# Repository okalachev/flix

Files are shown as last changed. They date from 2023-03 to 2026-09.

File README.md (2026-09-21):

<!-- markdownlint-disable MD041 -->

<p align="center">
  Flix logo<br>
  <b>Flix</b> (<i>flight + X</i>) — open source ESP32-based quadcopter made from scratch.
</p>

<table>
  <tr>
    <td align=center><strong>Version 1.1</strong> (3D-printed frame)</td>
    <td align=center><strong>Version 0</strong></td>
  </tr>
  <tr>
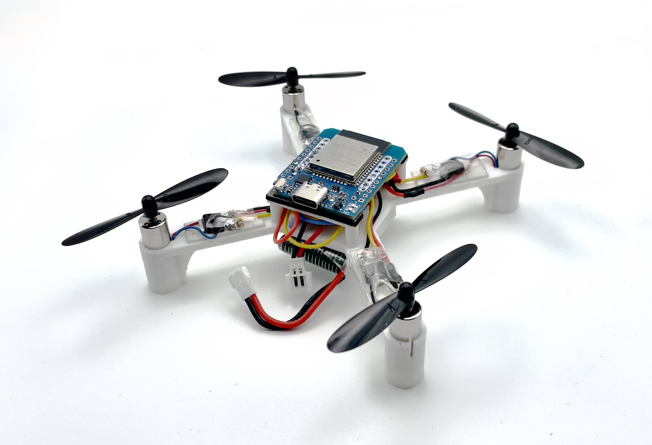
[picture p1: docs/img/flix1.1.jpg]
Flix quadcopter
    <td></td>
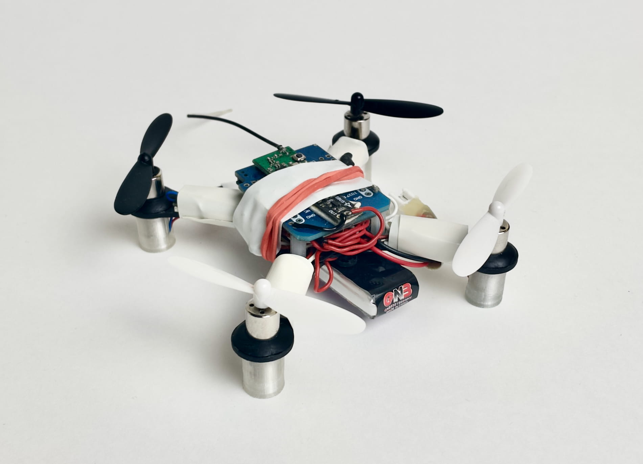
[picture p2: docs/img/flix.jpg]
Flix quadcopter
    <td></td>
  </tr>
</table>

## Features

* Dedicated for education and research.
* Made from general-purpose components.
* Simple and clean source code in Arduino (<2k lines firmware).
* Communication using MAVLink protocol over Wi-Fi or ESP-NOW.
* Control with USB gamepad, remote control or smartphone.
* Wireless command line interface and analyzing.
* Precise simulation with Gazebo.
* Python library for scripting and automatic flights.
* Textbook on flight control theory and practice ([in development](https://quadcopter.dev)).
* *Position control (planned)*.

## It actually flies

See detailed demo video: https://youtu.be/hT46CZ1CgC4.



Version 0 demo video: https://youtu.be/8GzzIQ3C6DQ.



Usage in education (RoboCamp 2025): https://youtu.be/Wd3yaorjTx0.



See the [user builds gallery](docs/user.md):

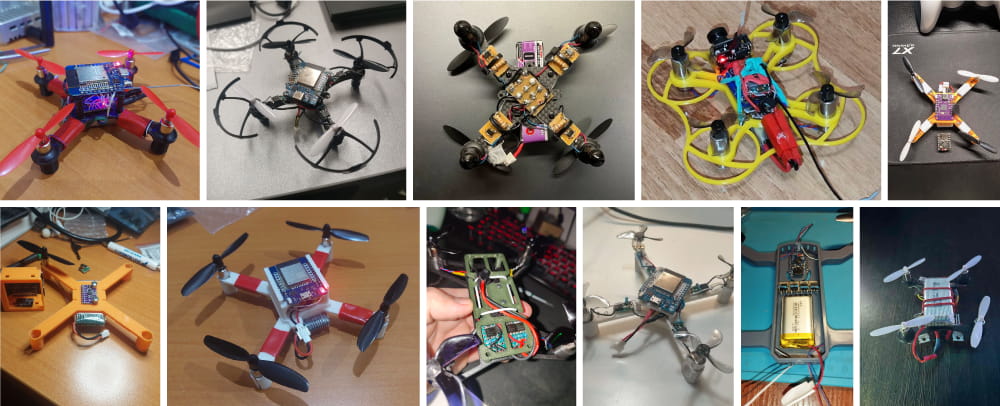
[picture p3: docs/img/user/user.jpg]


### PCB

The official PCB *(Flix2)* is in development now. Follow the [project's channel](https://t.me/opensourcequadcopter) to track the progress.

Outdoor flights demo video of the current prototype:



### Position control

The position control feature is in development. RoboCamp 2026 demo (using an overhead camera, [sources](https://github.com/xTimop/flix-poscontrol/compare/robolager2026...xTimop:flix-poscontrol:poscontrol)):



## Simulation

The simulator is implemented using Gazebo and runs the original Arduino code:

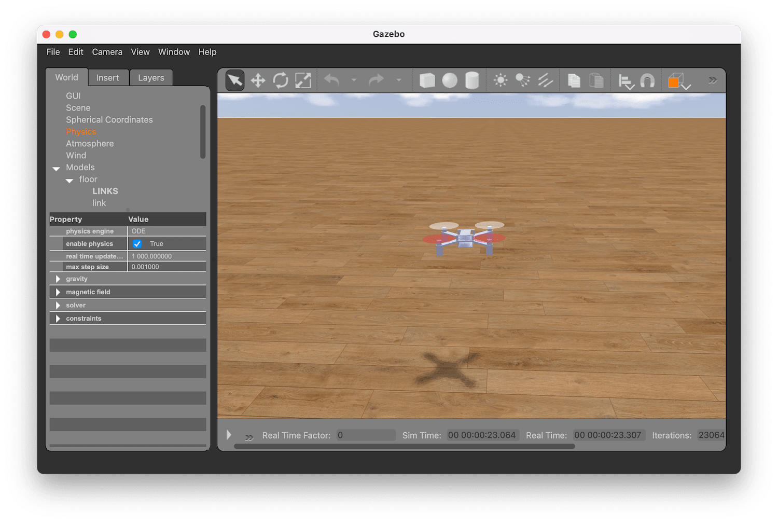
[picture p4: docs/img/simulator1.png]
Flix simulator


## Documentation articles

1. [Assembly instructions](docs/assembly.md).
2. [Usage: build, setup and flight](docs/usage.md).
3. [Simulation](gazebo/README.md).
4. [Python library](tools/pyflix/README.md).

Additional articles:

* [User builds gallery](docs/user.md).
* [Firmware architectural overview](docs/firmware.md).
* [Troubleshooting](docs/troubleshooting.md).
* [Log analysis](docs/log.md).

## Components

|Type|Part|Image|Quantity|
|-|-|:-:|:-:|
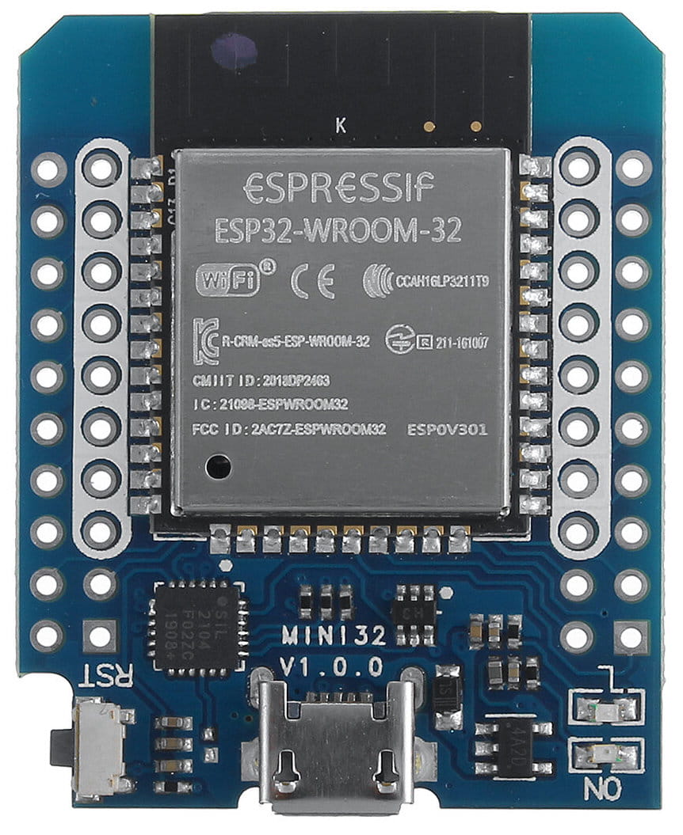
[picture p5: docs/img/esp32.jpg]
|Microcontroller board|ESP32 Mini.<br>ESP32-S3/ESP32-C3 boards are also supported.||1|
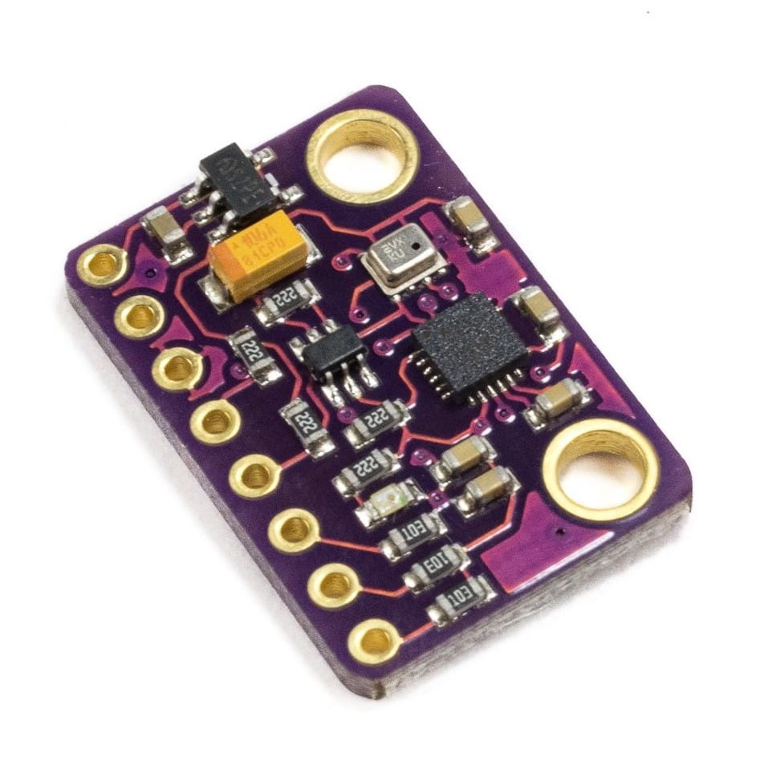
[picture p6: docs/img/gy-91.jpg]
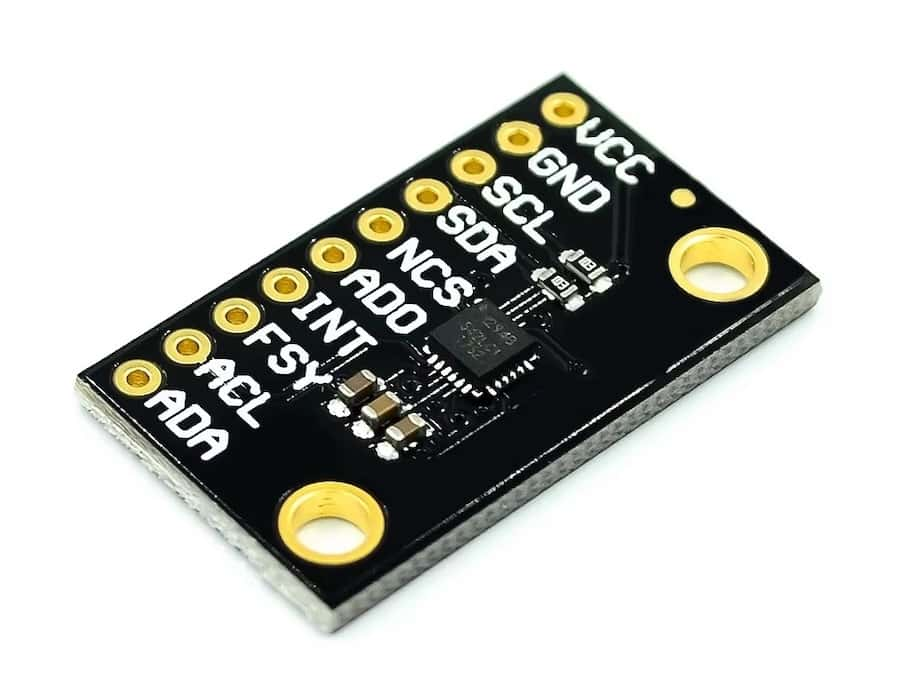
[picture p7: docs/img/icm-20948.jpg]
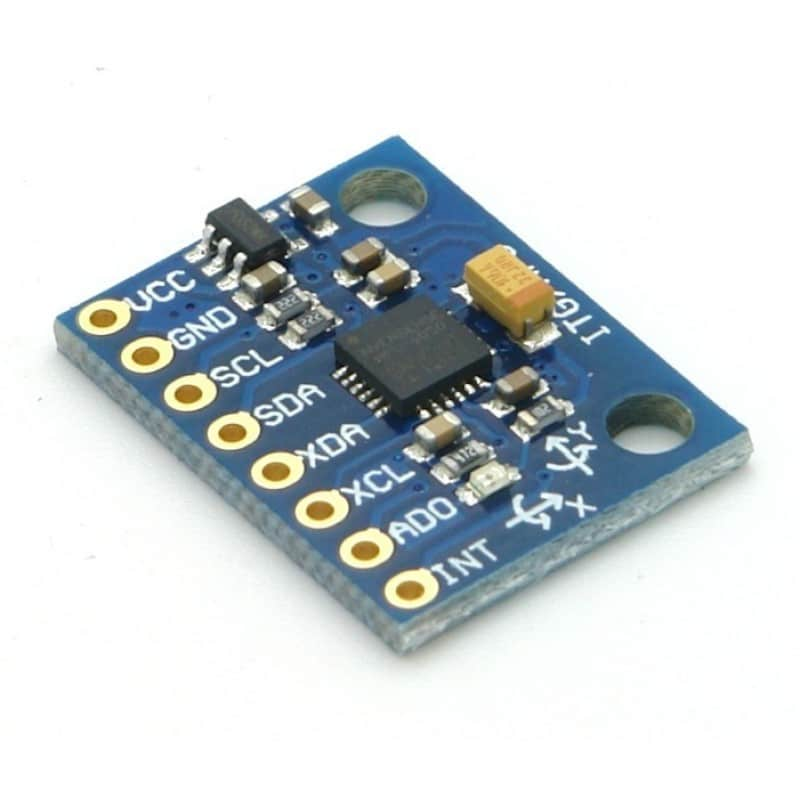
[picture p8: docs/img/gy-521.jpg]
|IMU (and barometer¹) board|GY‑91, MPU-9265 (or other MPU‑9250/MPU‑6500 board)<br>ICM20948V2 (ICM‑20948)<br>GY-521 (MPU-6050)|<br><br>|1|
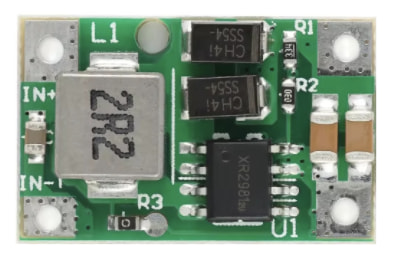
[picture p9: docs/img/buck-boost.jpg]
|*Boost converter (optional, for more stable power supply)*|*5V output*||1|
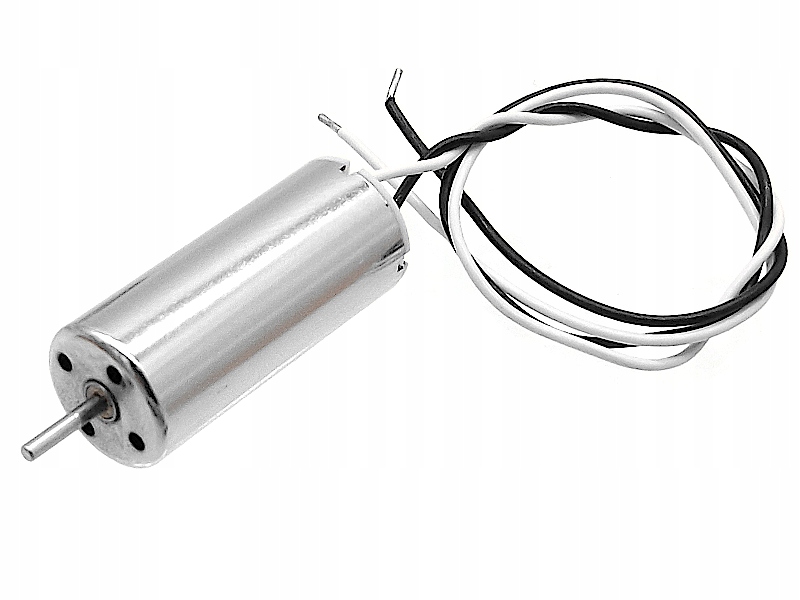
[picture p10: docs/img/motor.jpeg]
|Motor|8520 3.7V brushed motor.<br>Motor with exact 3.7V voltage is needed, not ranged working voltage (3.7V — 6V).<br>Make sure the motor shaft diameter and propeller hole diameter match!||4|
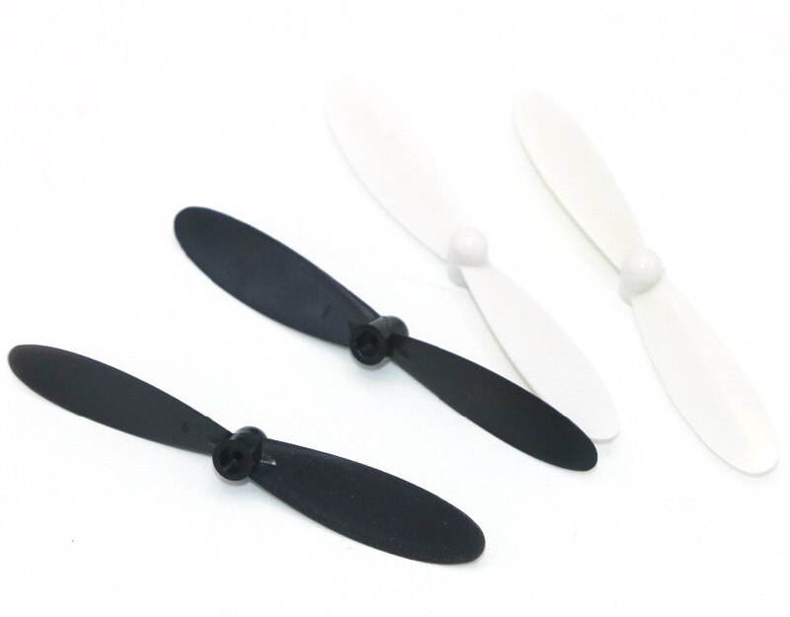
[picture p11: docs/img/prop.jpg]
|Propeller|55 mm or 65 mm||4|
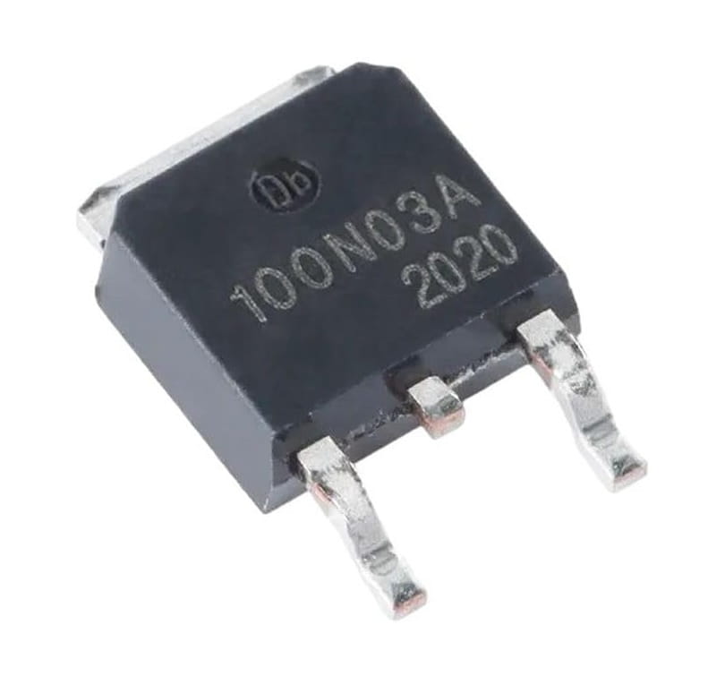
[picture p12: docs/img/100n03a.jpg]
|MOSFET (transistor)|UMW 100N03A or [analog](https://t.me/opensourcequadcopter/33).<br>Warning: don't use KIA 100N03A or other manufacturers, they might not work!||4|
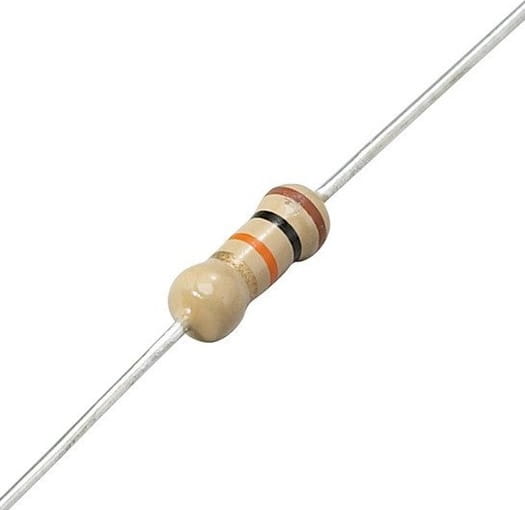
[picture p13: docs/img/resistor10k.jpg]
|Pull-down resistor<br>Voltage measurement resistor|10 kΩ||6|
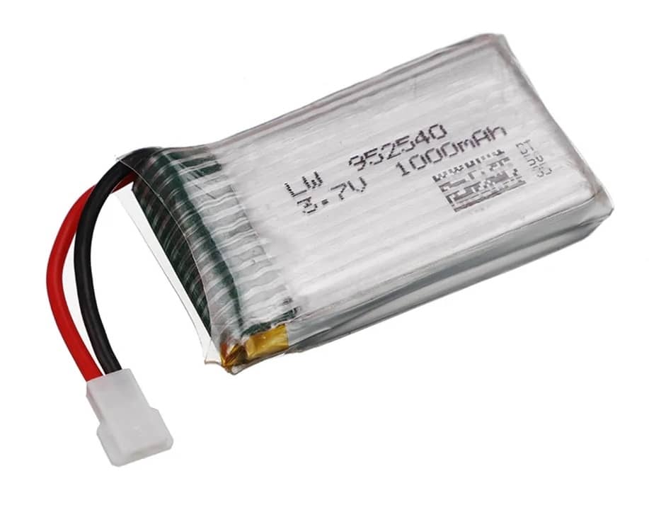
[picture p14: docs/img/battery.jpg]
|3.7V Li-Po battery|LW 952540 (or any compatible by the size).<br>Make sure the battery has enough discharge rate and capacity — 25C with 1000 mAh or more is recommended!||1|
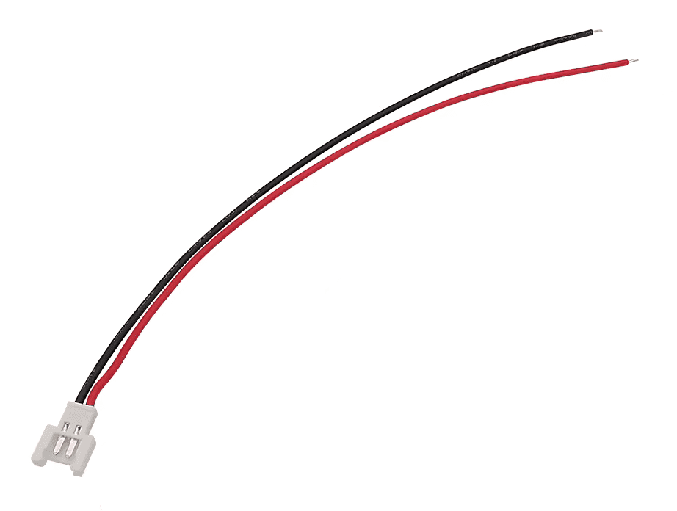
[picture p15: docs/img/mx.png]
|Battery connector cable|MX2.0 2P female||1|
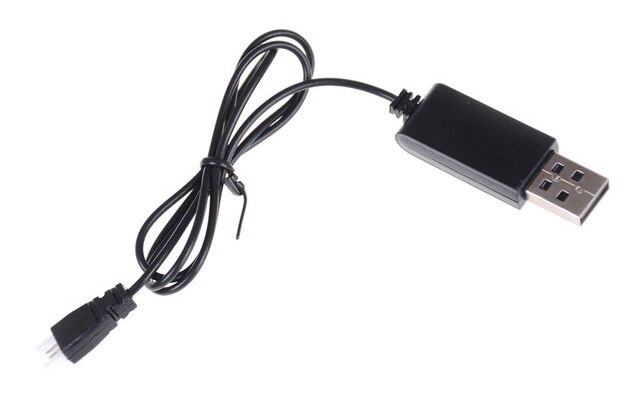
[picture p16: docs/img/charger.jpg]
|Li-Po Battery charger|Any||1|
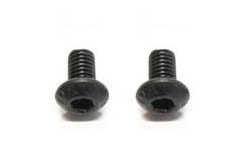
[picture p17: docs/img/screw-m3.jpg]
|Screws for IMU board mounting|M3x5||2|
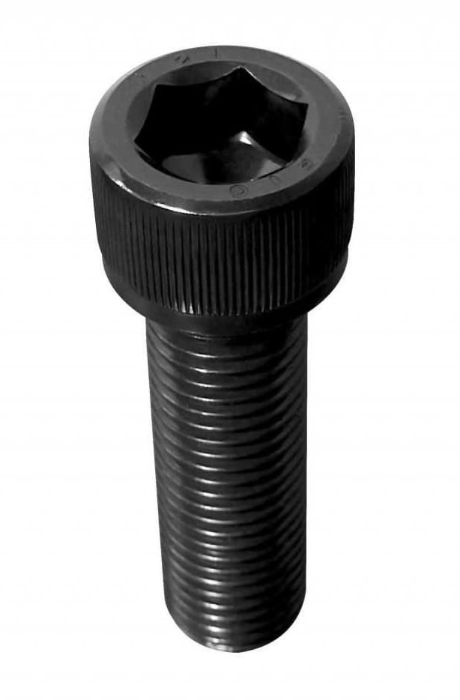
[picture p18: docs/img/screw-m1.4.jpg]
|Screws for frame assembly|M1.4x5||4|
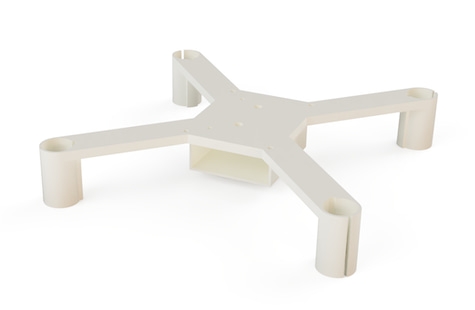
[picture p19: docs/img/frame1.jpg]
|Frame main part|3D printed²: [`stl`](docs/assets/flix-frame-1.1.stl) [`step`](docs/assets/flix-frame-1.1.step)<br>Recommended settings: layer 0.2 mm, line 0.4 mm, infill 100%.||1|
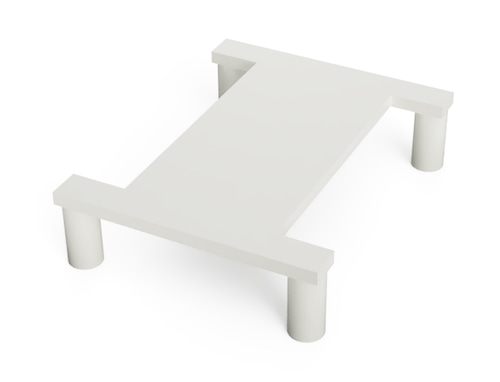
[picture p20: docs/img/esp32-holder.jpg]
|Frame top part|3D printed: [`stl`](docs/assets/esp32-holder.stl) [`step`](docs/assets/esp32-holder.step)||1|
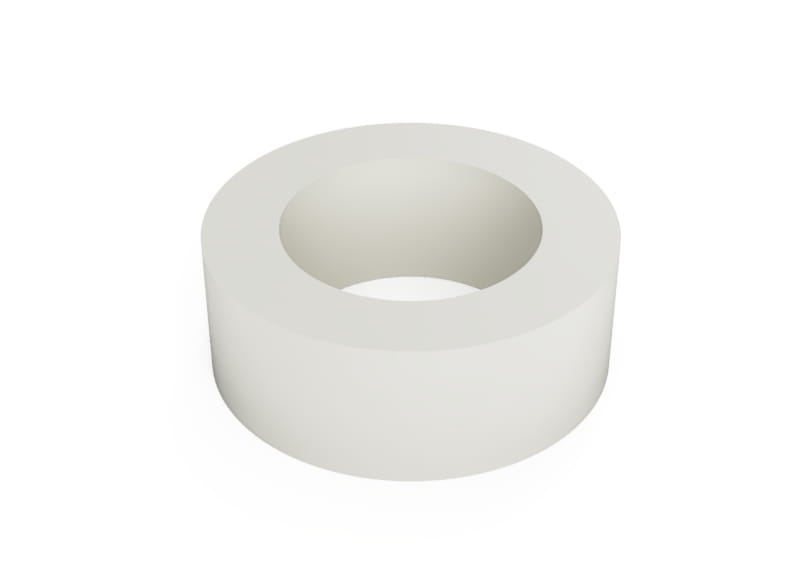
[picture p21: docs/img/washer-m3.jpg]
|Washer for IMU board mounting|3D printed: [`stl`](docs/assets/washer-m3.stl) [`step`](docs/assets/washer-m3.step)||2|
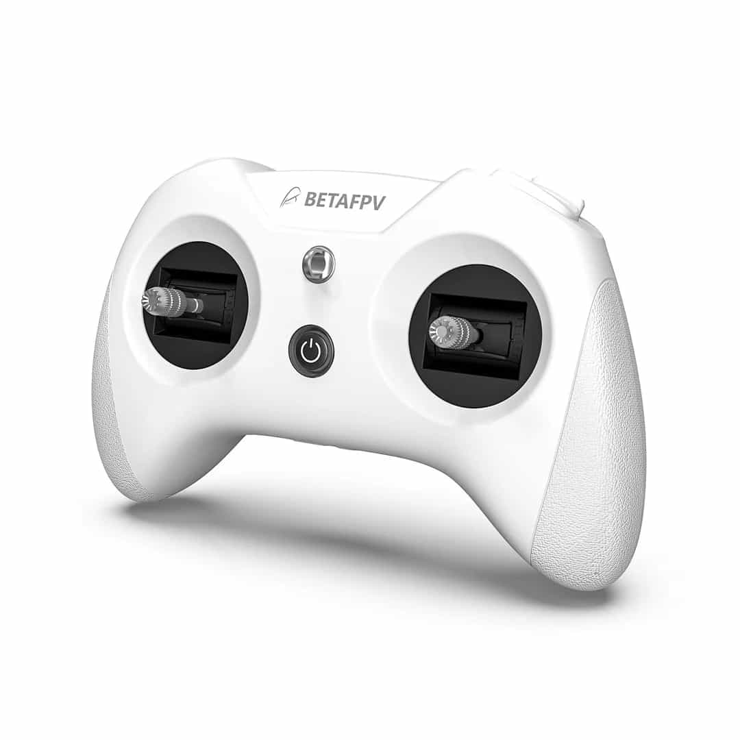
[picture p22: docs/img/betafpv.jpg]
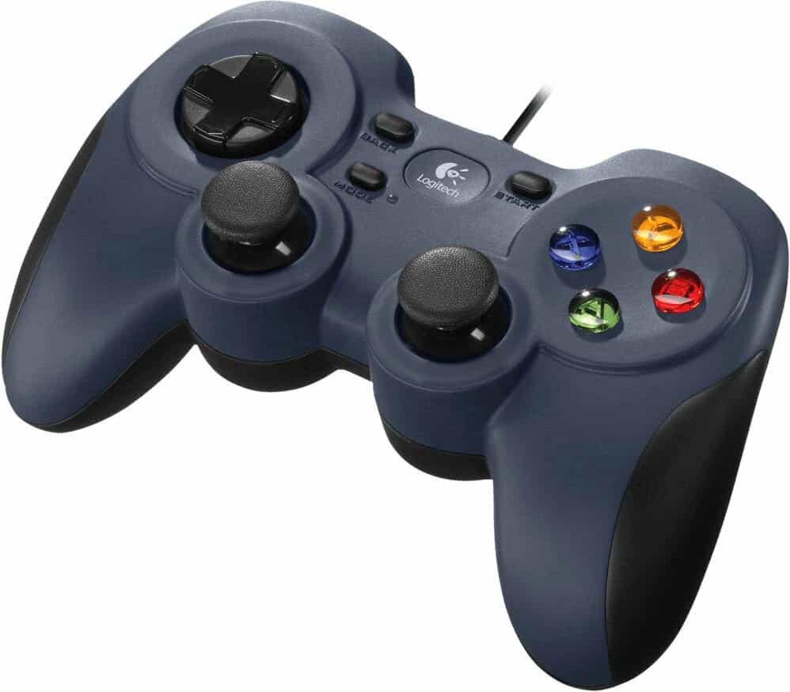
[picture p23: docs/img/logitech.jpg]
|Controller (recommended)|CC2500 transmitter, like BetaFPV LiteRadio CC2500 (RC receiver/Wi-Fi).<br>Two-sticks gamepad (Wi-Fi only) — see [recommended gamepads](https://docs.qgroundcontrol.com/master/en/qgc-user-guide/setup_view/joystick.html#supported-joysticks).<br>Other⁵||1|
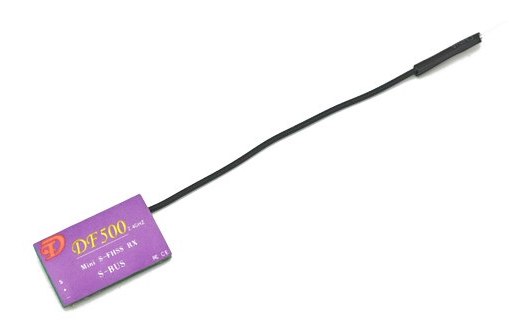
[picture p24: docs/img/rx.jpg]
|*RC receiver (optional)*|*DF500 or other³*||1|
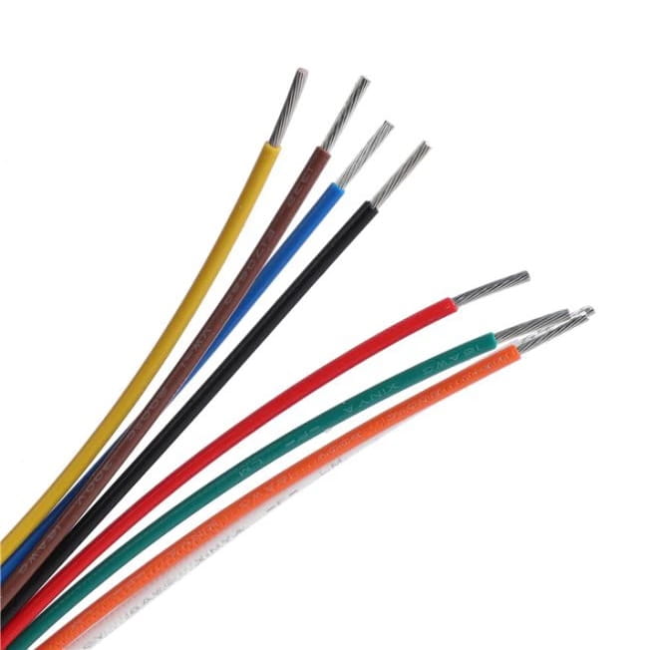
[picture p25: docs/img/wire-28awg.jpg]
|Wires|28 AWG recommended|||
|Tape, double-sided tape||||

*¹ — barometer is not used for now.*<br>
*² — this frame is optimized for GY-91 board, if using other, the board mount holes positions should be modified.*<br>
*³ — you also may use any transmitter-receiver pair with SBUS interface.*

Tools required for assembly:

* 3D printer.
* Soldering iron.
* Solder wire (with flux).
* Screwdrivers.
* Multimeter.

Feel free to modify the design and or code, and create your own improved versions. Send your results to the [official Telegram chat](https://t.me/opensourcequadcopterchat), or directly to the author ([E-mail](mailto:okalachev@gmail.com), [Telegram](https://t.me/okalachev)).

## Schematics

### Simplified connection diagram

Flix version 1 schematics

*(Dashed elements are optional).*

Motor connection scheme:

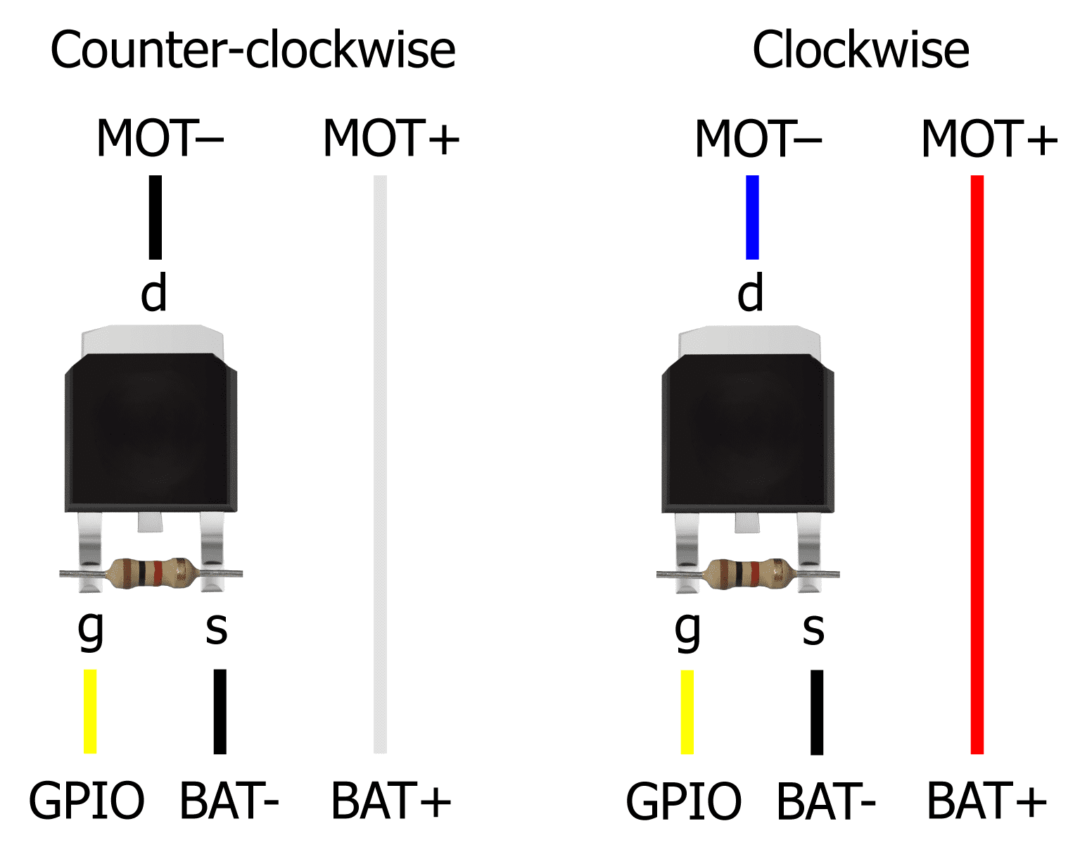
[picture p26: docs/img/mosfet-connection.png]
MOSFET connection scheme


You can see a user-contributed [variant of complete circuit diagram](https://miro.com/app/board/uXjVN-dTjoo=/?moveToWidget=3458764612338222067&cot=14) of the drone.

### Notes

* Power ESP32 Mini with Li-Po battery using VCC (+) and GND (-) pins.
* Connect the IMU board to the ESP32 Mini using VSPI, power it using 3.3V and GND pins:

  |IMU pin|ESP32 pin|
  |-|-|
  |GND|GND|
  |3.3V|3.3V|
  |SCL *(SCK)*|SVP (GPIO18)|
  |SDA *(MOSI)*|GPIO23|
  |SAO *(MISO)*|GPIO19|
  |NCS|GPIO5|

* Solder pull-down resistors to the MOSFETs.
* Connect the motors to the ESP32 Mini using MOSFETs, by following scheme:

  |Motor|Position|Direction|Prop type|Motor wires|GPIO|
  |-|-|-|-|-|-|
  |Motor 0|Rear left|Counter-clockwise|B|Black & White|GPIO12 *(TDI)*|
  |Motor 1|Rear right|Clockwise|A|Blue & Red|GPIO13 *(TCK)*|
  |Motor 2|Front right|Counter-clockwise|B|Black & White|GPIO14 *(TMS)*|
  |Motor 3|Front left|Clockwise|A|Blue & Red|GPIO15 *(TD0)*|

  Clockwise motors have blue & red wires and correspond to propeller type A (marked on the propeller).
  Counter-clockwise motors have black & white wires correspond to propeller type B.

* Optionally connect the RC receiver to the ESP32's UART2:

  |Receiver pin|ESP32 pin|
  |-|-|
  |GND|GND|
  |VIN|VCC (or 3.3V depending on the receiver)|
  |Signal (TX)|GPIO4|

* Optionally connect the battery voltage divider for voltage monitoring to any ADC1 pin (e. g. *GPIO32* on ESP32, *GPIO3* on ESP32-S3).

  ESP32 and ESP32-S3 [can measure](https://docs.espressif.com/projects/arduino-esp32/en/latest/api/adc.html#analogsetattenuation) up to 3.1 V and ESP32-S3/ESP32-C3 can measure up to 2.5 V, so choose the voltage divider resistors accordingly.

## Resources

* Telegram channel on developing the drone and the flight controller (in Russian): https://t.me/opensourcequadcopter.
* Official Telegram chat: https://t.me/opensourcequadcopterchat (English / Russian).
* Detailed article on Habr.com about the development of the drone (in Russian): https://habr.com/ru/articles/814127/.

## Disclaimer

This is a DIY project, and I hope you find it interesting and useful. However, it's not easy to assemble and set up, and it's provided "as is" without any warranties. There's no guarantee that it will work perfectly, or even work at all.

⚠️ The author is not responsible for any damage, injury, or loss resulting from the use of this project. Use at your own risk!

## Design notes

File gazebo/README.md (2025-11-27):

# Simulation

The Flix drone simulator is based on Gazebo 11 and runs the firmware code in virtual physical environment.

Gazebo 11 works on **Ubuntu 20.04** and used to work on macOS. However, on the recent macOS versions it seems to be broken, so Ubuntu 20.04 is recommended.

Flix simulator running on macOS

## Installation

1. Clone the Flix repository using it:

   ```bash
   git clone https://github.com/okalachev/flix.git && cd flix
   ```

2. Install Arduino CLI:

   ```bash
   curl -fsSL https://raw.githubusercontent.com/arduino/arduino-cli/master/install.sh | BINDIR=~/.local/bin sh
   ```

3. Install Gazebo 11:

   ```bash
   sudo sh -c 'echo "deb http://packages.osrfoundation.org/gazebo/ubuntu-stable `lsb_release -cs` main" > /etc/apt/sources.list.d/gazebo-stable.list'
   wget https://packages.osrfoundation.org/gazebo.key -O - | sudo apt-key add -
   sudo apt-get update
   sudo apt-get install -y gazebo11 libgazebo11-dev
   ```

   Set up your Gazebo environment variables:

   ```bash
   echo "source /usr/share/gazebo/setup.sh" >> ~/.bashrc
   source ~/.bashrc
   ```

4. Install SDL2 and other dependencies:

   ```bash
   sudo apt-get update && sudo apt-get install build-essential libsdl2-dev
   ```

5. Add your user to the `input` group to enable joystick support (you need to re-login after this command):

   ```bash
   sudo usermod -a -G input $USER
   ```

6. Run the simulation:

   ```bash
   make simulator
   ```

## Usage

Just like the real drone, the simulator can be controlled using a USB remote control or a smartphone.

### Control with smartphone

1. Install [QGroundControl mobile app](https://docs.qgroundcontrol.com/master/en/qgc-user-guide/getting_started/download_and_install.html#android) on your smartphone. For **iOS**, use [QGroundControl build from TAJISOFT](https://apps.apple.com/ru/app/qgc-from-tajisoft/id1618653051).
2. Connect your smartphone to the same Wi-Fi network as the machine running the simulator.
3. If you're using a virtual machine, make sure that its network is set to the **bridged** mode with Wi-Fi adapter selected.
4. Run the simulation.
5. Open QGroundControl app. It should connect and begin showing the virtual drone's telemetry automatically.
6. Go to the settings and enable *Virtual Joystick*. *Auto-Center Throttle* setting **should be disabled**.
7. Use the virtual joystick to fly the drone!

> [!TIP]
> Decrease `CTL_TILT_MAX` parameter when flying using the smartphone to make the controls less sensitive.

### Control with USB remote control

1. Connect your USB remote control to the machine running the simulator.
2. Run the simulation.
3. Calibrate the RC using `cr` command in the command line interface.
4. Use the USB remote control to fly the drone!

### Piloting

To start the flight, arm the drone moving the throttle stick to the bottom right position:



To disarm, move the throttle stick to the bottom left position:



See other piloting and usage details in general [usage article](../docs/usage.md).

## Code structure

Flix simulator consists of the following components:

* Physical model of the drone in Gazebo format: [`models/flix/flix.sdf`](models/flix/flix.sdf).
* Plugin for Gazebo: [`simulator.cpp`](simulator.cpp). The plugin is attached to the physical model. It receives stick positions from the controller, gets the data from the virtual sensors, and then passes this data to the Arduino code.
* Arduino emulation: [`Arduino.h`](Arduino.h). This file contains partial implementation of the Arduino API, that is working within Gazebo plugin environment.

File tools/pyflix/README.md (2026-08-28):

# Flix Python library

The Flix Python library allows you to remotely connect to a Flix quadcopter. It provides access to telemetry data, supports executing console commands, and controlling the drone's flight.

To use the library, connect to the drone's Wi-Fi. To use it with the simulator, ensure the script runs on the same network as the simulator.

## Installation

If you have cloned the [repo](https://github.com/okalachev/flix), install the library from the repo:

```bash
cd /path/to/flix/repo
pip install -e tools
```

Alternatively, install from pip:

```bash
pip install pyflix
```

## Usage

The API is accessed through the `Flix` class:

```python
from pyflix import Flix
flix = Flix()  # create a Flix object and wait for connection
```

If using ESP-NOW connection, specify the proxy device name in `FLIX_DEVICE` environment variable or pass it to the constructor: `Flix(device='/dev/cu.usbserial-0001')`.

### Telemetry

Basic telemetry is available through object properties. The property names generally match the corresponding variables in the firmware code:

```python
print(flix.connected)       # True if connected to the drone
print(flix.mode)            # current flight mode (str)
print(flix.armed)           # True if the drone is armed
print(flix.landed)          # True if the drone is landed
print(flix.voltage)         # battery voltage (NaN - unknown, ~0 - USB powered)
print(flix.attitude)        # attitude quaternion [w, x, y, z]
print(flix.attitude_euler)  # attitude as Euler angles [roll, pitch, yaw]
print(flix.rates)           # angular rates [roll_rate, pitch_rate, yaw_rate]
print(flix.channels)        # raw RC channels (list)
print(flix.motors)          # motor outputs (list)
print(flix.acc)             # accelerometer output (list)
print(flix.gyro)            # gyroscope output (list)
```

The library uses the Front-Left-Up coordinate system — the same as the firmware:



All angles are in radians.

### Events

The Flix object implements the *Observable* pattern, allowing to listen for events. You can subscribe to events using `on` method:

```python
flix.on('connected', lambda: print('Connected to Flix'))
flix.on('disconnected', lambda: print('Disconnected from Flix'))
flix.on('print', lambda text: print(f'Flix says: {text}'))
```

Unsubscribe from events using `off` method:

```python
flix.off('print')  # unsubscribe from print events
flix.off(callback)  # unsubscribe specific callback
```

You can also wait for specific events using `wait` method. This method returns the data associated with the event:

```python
gyro = flix.wait('gyro')  # wait for gyroscope update
attitude = flix.wait('attitude', timeout=3)  # wait for attitude update, raise TimeoutError after 3 seconds
```

The second argument (`value`) specifies a condition for filtering events. It can be either an expected value or a callable:

```python
flix.wait('armed', True)  # wait until armed
flix.wait('armed', False)  # wait until disarmed
flix.wait('mode', 'AUTO')  # wait until flight mode is switched to AUTO
flix.wait('motors', lambda motors: not any(motors))  # wait until all motors stop
flix.wait('attitude_euler', lambda att: att[0] > 0)  # wait until roll angle is positive
```

Full list of events:

|Event|Description|Associated data|
|-----|---|---|
|`connected`|Connected to the drone||
|`disconnected`|Connection is lost||
|`armed`|Armed state update|Armed state *(bool)*|
|`mode`|Flight mode update|Flight mode *(str)*|
|`landed`|Landed state update|Landed state *(bool)*|
|`voltage`|Battery voltage update|Voltage *(float)*|
|`print`|The drone prints text to the console|Text|
|`attitude`|Attitude update|Attitude quaternion *(list)*|
|`attitude_euler`|Attitude update|Euler angles *(list)*|
|`rates`|Angular rates update|Angular rates *(list)*|
|`channels`|Raw RC channels update|Raw RC channels *(list)*|
|`motors`|Motor outputs update|Motor outputs *(list)*|
|`acc`|Accelerometer update|Accelerometer output *(list)*|
|`gyro`|Gyroscope update|Gyroscope output *(list)*|
|`mavlink`|Received MAVLink message|Message object|
|`mavlink.<message_name>`|Received specific MAVLink message|Message object|
|`mavlink.<message_id>`|Received specific MAVLink message|Message object|
|`value`|Named value update (see below)|Name, value|
|`value.<name>`|Specific named value update (see below)|Value|

> [!NOTE]
> Update events trigger on every new piece of data from the drone, and do not mean the value has changed.

### Basic methods

Get and set firmware parameters using `get_param` and `set_param` methods:

```python
pitch_p = flix.get_param('CTL_ATT_P_P')  # get parameter value
flix.set_param('CTL_ATT_P_P', 5)         # set parameter value
```

Execute console commands using `cli` method. This method returns the command response:

```python
imu = flix.cli('imu')    # get detailed IMU data
time = flix.cli('time')  # get detailed time data
flix.cli('reboot')       # reboot the drone
```

> [!TIP]
> Use `help` command to get the list of available commands.

You can arm and disarm the drone using `set_armed` method (warning: the drone will fall if disarmed in the air):

```python
flix.set_armed(True)   # arm the drone
flix.set_armed(False)  # disarm the drone
```

You can pass pilot's controls using `set_controls` method:

```python
flix.set_controls(roll=0, pitch=0, yaw=0, throttle=0.6)
```

> [!WARNING]
> This method **is not intended for automatic flights**, only for adding support for a custom pilot input device.

### Automatic flight

To perform automatic flight, switch the mode to *AUTO*, either from the remote control, or from the code:

```python
flix.set_mode('AUTO')
```

In this mode you can set flight control targets. Setting attitude target:

```python
flix.set_attitude([0.1, 0.2, 0.3], 0.6)  # set target roll, pitch, yaw and thrust
flix.set_attitude([1, 0, 0, 0], 0.6)  # set target attitude quaternion and thrust
```

Setting angular rates target:

```python
flix.set_rates([0.1, 0.2, 0.3], 0.6)  # set target roll rate, pitch rate, yaw rate and thrust
```

You also can control raw motor outputs directly:

```python
flix.set_motors([0.5, 0.5, 0.5, 0.5])  # set motor outputs in range [0, 1]
```

In *AUTO* mode, the drone will arm automatically if the thrust is greater than zero, and disarm if thrust is zero. Therefore, to disarm the drone, set thrust to zero:

```python
flix.set_attitude([0, 0, 0], 0)  # disarm the drone
```

The following methods are in development and are not functional yet:

* `set_position` — set target position.
* `set_velocity` — set target velocity.

To exit *AUTO* mode move control sticks and the drone will switch to *STAB* mode.

## Usage alongside QGroundControl

You can use the Flix library alongside the QGroundControl app, using proxy mode. To do that:

1. Run proxy for `pyflix` and QGroundControl in background:

   ```bash
   flix-proxy
   ```

2. Go to QGroundControl settings ⇒ *Comm Links*.
3. Add new link with the following settings:
   * *Name*: Proxy
   * *Automatically Connect on Start*: ✓
   * *Type*: UDP
   * *Port*: 14560
4. Restart QGroundControl.

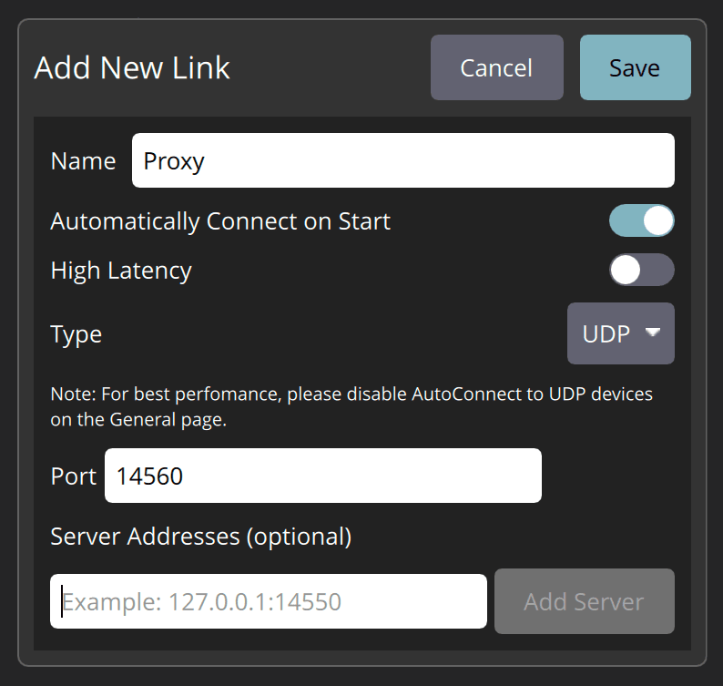
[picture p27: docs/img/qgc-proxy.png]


Now you can run `pyflix` scripts and QGroundControl simultaneously.

## Tools

The following scripts demonstrate how to use the library:

* [`cli.py`](../cli.py) — remote access to the drone's command line interface.
* [`log.py`](../log.py) — download flight logs from the drone.
* [`example.py`](../example.py) — a simple example, prints telemetry data and waits for events.

> [!TIP]
> Set `FLIX_DEVICE` environment variable to use these tools with ESP-NOW connection, for example:
>
> ```bash
> FLIX_DEVICE=/dev/cu.usbserial-0001 tools/cli.py
> ```

## Advanced usage

### MAVLink

You can access the most recently received messages using `messages` property:

```python
print(flix.messages.get('HEARTBEAT'))  # print the latest HEARTBEAT message
```

You can wait for a specific message using `wait` method:

```python
heartbeat = flix.wait('mavlink.HEARTBEAT')
```

You can send raw messages using `mavlink` property:

```python
from pymavlink.dialects.v20 import common as mavlink

flix.mavlink.heartbeat_send(mavlink.MAV_TYPE_GCS, mavlink.MAV_AUTOPILOT_INVALID,
                            mavlink.MAV_MODE_FLAG_CUSTOM_MODE_ENABLED, 0, 0)
```

### Named values

You can pass arbitrary named values from the firmware to the Python script using `NAMED_VALUE_FLOAT`, `NAMED_VALUE_INT`, `DEBUG`, `DEBUG_VECT`, and `DEBUG_FLOAT_ARRAY` MAVLink messages.

All these named values will appear in the `values` dictionary:

```python
print(flix.values['some_value'])
print(flix.values['some_vector'])
```

You can send values from the firmware like this (`mavlink.ino`):

```cpp
// Send float named value
mavlink_msg_named_value_float_pack(SYSTEM_ID, MAV_COMP_ID_AUTOPILOT1, &msg, t, "loop_rate", loopRate);
sendMessage(&msg);

// Send vector named value
mavlink_msg_debug_vect_pack(SYSTEM_ID, MAV_COMP_ID_AUTOPILOT1, &msg, "gyro_bias", t, gyroBias.x, gyroBias.y, gyroBias.z);
sendMessage(&msg);
```

### Logging

You can control Flix library verbosity using Python's `logging` module:

```python
import logging

logger = logging.getLogger('flix')
logger.setLevel(logging.DEBUG)  # be more verbose
logger.setLevel(logging.WARNING)  # be less verbose
```

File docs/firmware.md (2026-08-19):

# Firmware overview

The firmware is a regular Arduino sketch, and it follows the classic Arduino one-threaded design. The initialization code is in the `setup()` function, and the main loop is in the `loop()` function. The sketch includes several files, each responsible for a specific subsystem.

## Dataflow

Firmware dataflow diagram

The main loop is running at 1000 Hz. The dataflow goes through global variables, including:

* `t` *(float)* — current step time, *s*.
* `dt` *(float)* — time delta between the current and previous steps, *s*.
* `gyro` *(Vector)* — data from the gyroscope, *rad/s*.
* `acc` *(Vector)* — acceleration data from the accelerometer, *m/s<sup>2</sup>*.
* `rates` *(Vector)* — filtered angular rates, *rad/s*.
* `attitude` *(Quaternion)* — estimated attitude (orientation) of drone.
* `controlRoll`, `controlPitch`, `controlYaw`, `controlThrottle`, `controlMode` *(float)* — pilot control inputs, range [-1, 1].
* `motors` *(float[4])* — motor outputs, range [0, 1].

## Source files

Firmware source files are located in `flix` directory.

* [`flix.ino`](../flix/flix.ino) — Arduino sketch main file, entry point.Includes some global variable definitions and the main loop.
* [`imu.ino`](../flix/imu.ino) — reading data from the IMU sensor (gyroscope and accelerometer), IMU calibration.
* [`rc.ino`](../flix/rc.ino) — reading data from the RC receiver, RC calibration.
* [`estimate.ino`](../flix/estimate.ino) — attitude estimation, complementary filter.
* [`control.ino`](../flix/control.ino) — control subsystem, three-dimensional two-level cascade PID controller.
* [`motors.ino`](../flix/motors.ino) — PWM motor output control.
* [`mavlink.ino`](../flix/mavlink.ino) — interaction with QGroundControl or [pyflix](../tools/pyflix) via MAVLink protocol.
* [`console.ino`](../flix/console.ino) — serial and MAVLink console.

Utility files:

* [`vector.h`](../flix/vector.h), [`quaternion.h`](../flix/quaternion.h) — vector and quaternion libraries.
* [`pid.h`](../flix/pid.h) — generic PID controller.
* [`filter.h`](../flix/filter.h) — generic low-pass filter.

### Control subsystem

Pilot inputs are interpreted in `interpretControls()`, and then converted to the **control command**, which consists of the following:

* `attitudeTarget` *(Quaternion)* — target attitude of the drone.
* `ratesTarget` *(Vector)* — target angular rates, *rad/s*.
* `ratesExtra` *(Vector)* — additional (feed-forward) angular rates, used for yaw rate control in STAB mode, *rad/s*.
* `torqueTarget` *(Vector)* — target torque, range [-1, 1].
* `thrustTarget` *(float)* — collective motor thrust target, range [0, 1].

Control command is handled in `controlAttitude()`, `controlRates()`, `controlTorque()` functions. Each function may be skipped if the corresponding control target is set to `NAN`.

Control subsystem diagram

Armed state is stored in `armed` variable, and current mode is stored in `mode` variable.

### Console

To write into the console, `print()` function is used. This function sends data both to the Serial console and to the MAVLink console (which can be accessed wirelessly in QGroundControl). The function supports formatting:

```cpp
print("Test value: %.2f\n", testValue);
```

In order to add a console command, modify the `doCommand()` function in `console.ino` file.

> [!IMPORTANT]
> Avoid using delays in in-flight commands, it will **crash** the drone! (The design is one-threaded.)
>
> For on-the-ground commands, use `pause()` function, instead of `delay()`. This function allows to pause in a way that MAVLink connection will continue working.

### Parameter subsystem

Parameters subsystem (`parameters.ino`) uses standard [Preferences.h](https://docs.espressif.com/projects/arduino-esp32/en/latest/tutorials/preferences.html) ESP32 library to store parameters in non-volatile memory. Each parameter is a regular global variable, which is registered in the `parameters` array.

To add a new parameter:

1. Define a global variable for the parameter, two types are supported: `float` and `int`.
2. Add an entry to the `parameters` array, with the parameter name, a pointer to the variable, and optionally a callback function to call when the parameter is changed.
3. Everything else will be handled automatically.

See examples of adding new parameters in commits: [c434107](https://github.com/okalachev/flix/commit/c434107), [a687303](https://github.com/okalachev/flix/commit/a687303).

> [!NOTE]
> Since all the parameters are internally stored and passed as floats, the safe range for `int` parameters is -16777216 to 16777215.

## Adding a subsystem

To add a new subsystem:

1. Create a new `*.ino` file for your subsystem.
2. Define setup and loop functions for the subsystem, for example `setupMySubsystem()` and `loopMySubsystem()`.
3. Use `Rate` class if you need to limit the loop frequency, for example:

    ```cpp
    Rate mySubsystemRate(100); // 100 Hz

    void loopMySubsystem() {
    	if (!mySubsystemRate) return;
    	// Do something...
    }
4. Add setup and loop calls in to `setup()` and `loop()` functions in `flix.ino`.

## Building the firmware

See build instructions in [usage.md](usage.md).

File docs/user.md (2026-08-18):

# Hall of fame

This page contains user-built drones based on the Flix project. Publish your projects into the official Telegram-chat: [@opensourcequadcopterchat](https://t.me/opensourcequadcopterchat) or send materials as a pull request.

## RoboCamp 2026

<p align=center>
	  
</p>

The second Flix RoboCamp event took place in July 2026 in Saint Petersburg. The main goal for the competitors was to build a Flix-based quadcopter and implement **autonomous position control** using distance sensors and an overhead camera. Several participants were able to implement altitude hold, and two participants implemented stable position hold.

### Highlights

The winning project performed an automatic takeoff, stable position hold (2 min+), and navigation to a point selected by the user by clicking on the camera image.

See the demonstration video:



---

Author: [Oleg1405](https://t.me/Oleg1405).<br>
Description: ESP32 Mini, MPU-6500 IMU, boost converter, BT2.0 power connector, 65 mm props, BetaFPV ELRS Lite Receiver, Radiomaster Pocket + Mavlink Joystick (Android) control.

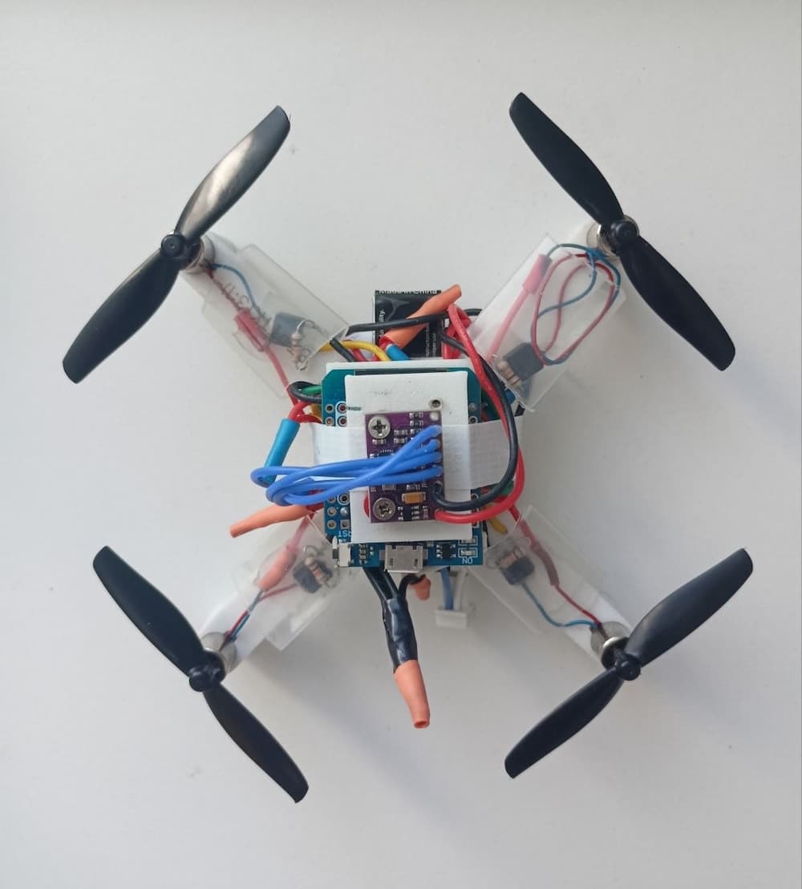
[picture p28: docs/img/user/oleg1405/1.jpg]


[Flight video](https://www.youtube.com/shorts/rbXV4sHbpso).

---

Author: Alican Erüst.<br>
Description: QX95 mm frame, 55 mm propellers, 3.7 V 25C 1050 mAh LiPo battery, MPU6050 IMU, Logitech F310 gamepad controller, with a total quadcopter weight of 66 g.

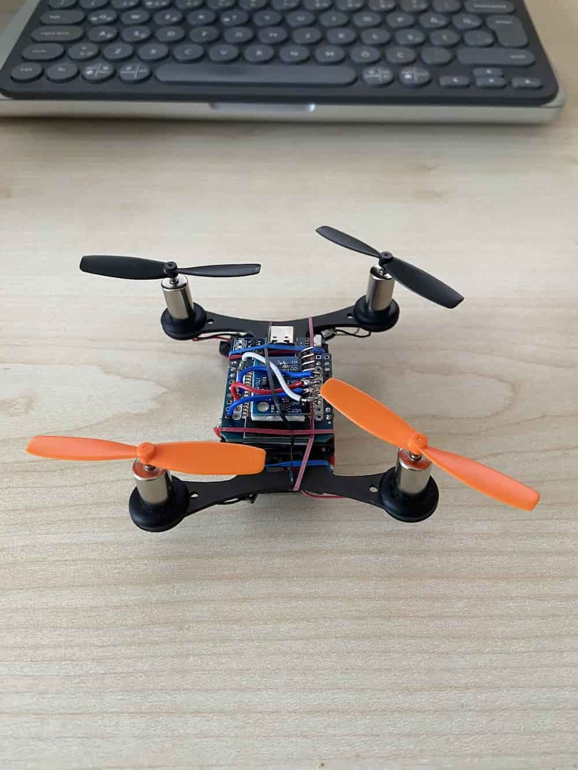
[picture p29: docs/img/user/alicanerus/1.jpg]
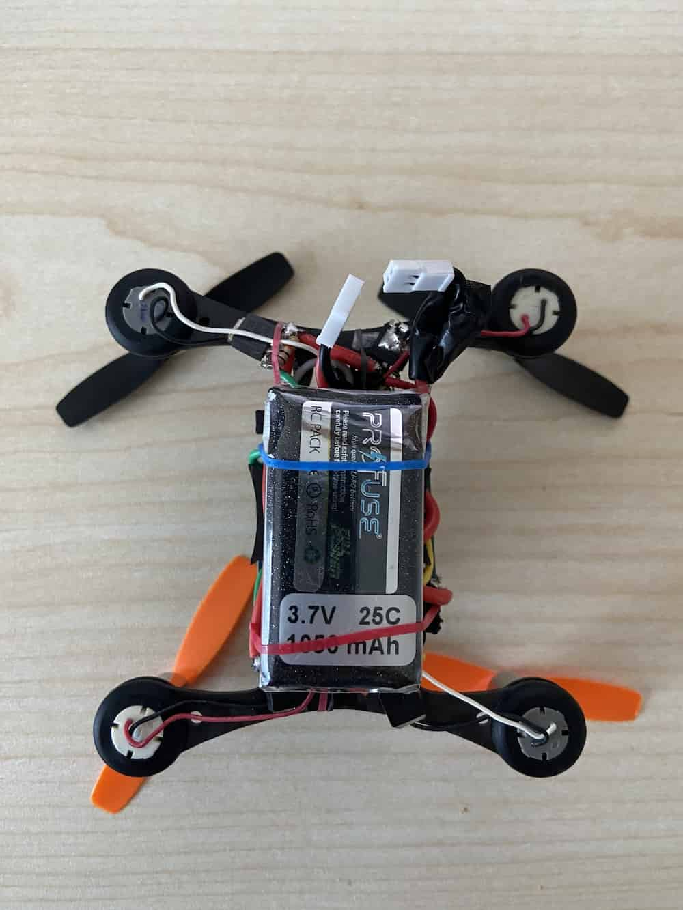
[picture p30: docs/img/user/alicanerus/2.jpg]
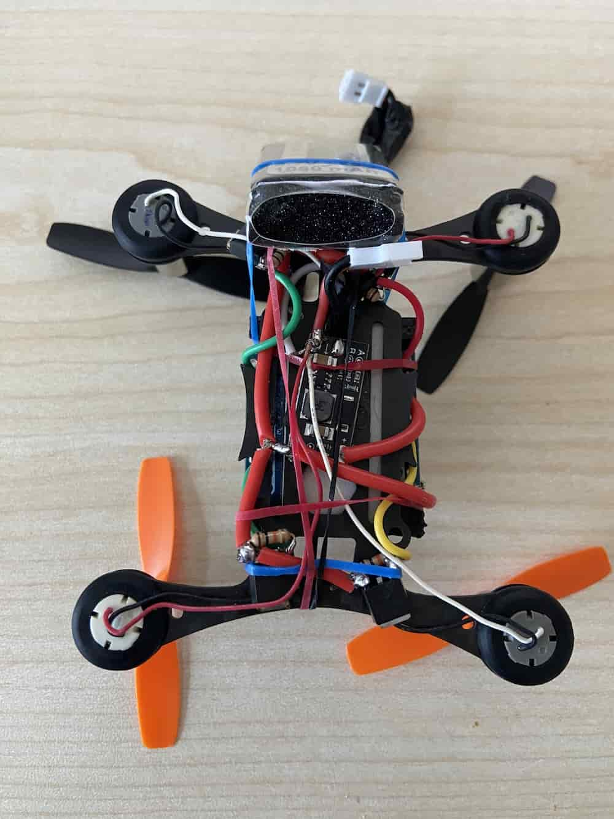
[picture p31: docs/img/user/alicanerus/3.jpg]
  

[Flight video](https://drive.google.com/file/d/1k0WeWTKnCAfaugkX7LcmNxsUuq79RL8Z/view?usp=sharing).

---

Author: [Неруш Михаил](https://t.me/NerushMV).<br>
Description: custom frame made of 4 mm plywood, 8520 brushed motors, 75 mm propellers, MPU-6500. FlySky FS-i6X with ESP32-based adapter for ESP-NOW communication (using PPM output).<br>
Sources and materials: [link](https://drive.google.com/drive/folders/1uWiDcuorLrtVs_IIR7Y13omij-7Q1nx8).

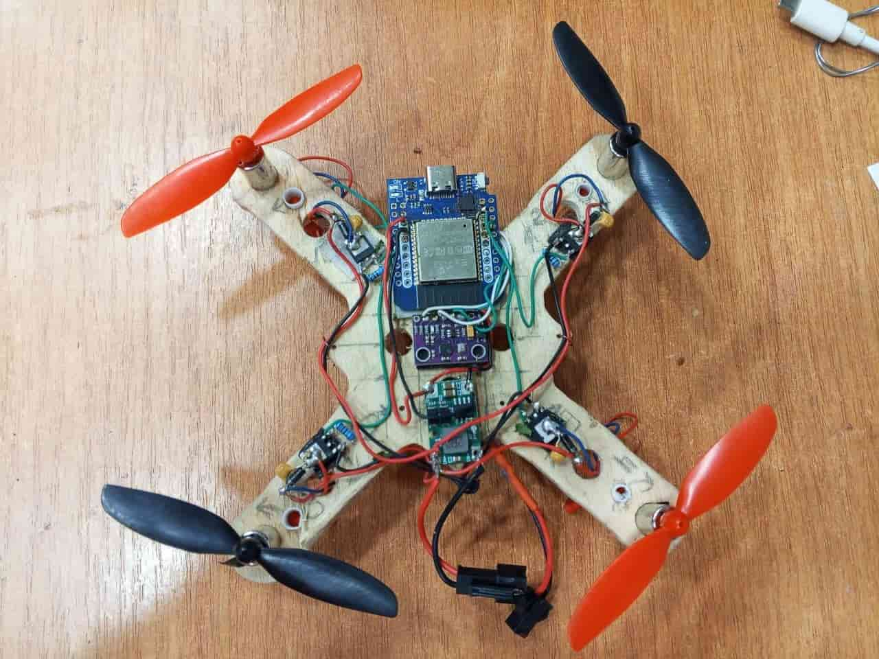
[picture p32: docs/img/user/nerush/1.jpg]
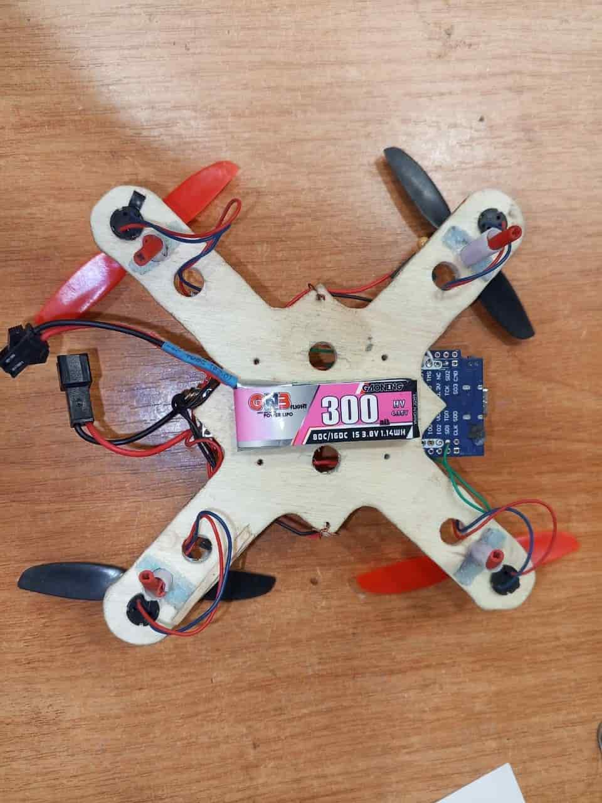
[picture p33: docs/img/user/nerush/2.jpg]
 

[Flight video](https://drive.google.com/file/d/1jRXeGx34lJpUfw0GKLQeIzkWZvooQJSE/view?usp=sharing).

---

Author: [Konstantinos Paraskevas](https://github.com/Frapais).<br>
Description: drone with a custom single-boarded airframe, extending the [Sprig-C3 module](https://github.com/Frapais/Sprig-C3).
ESP32-C3 microcontroller, ICM-20948 IMU, on-board fuel-gauge, status LED indicator.<br>
Repository with all the code and PCB sources: https://github.com/Frapais/Sprig-Drone.

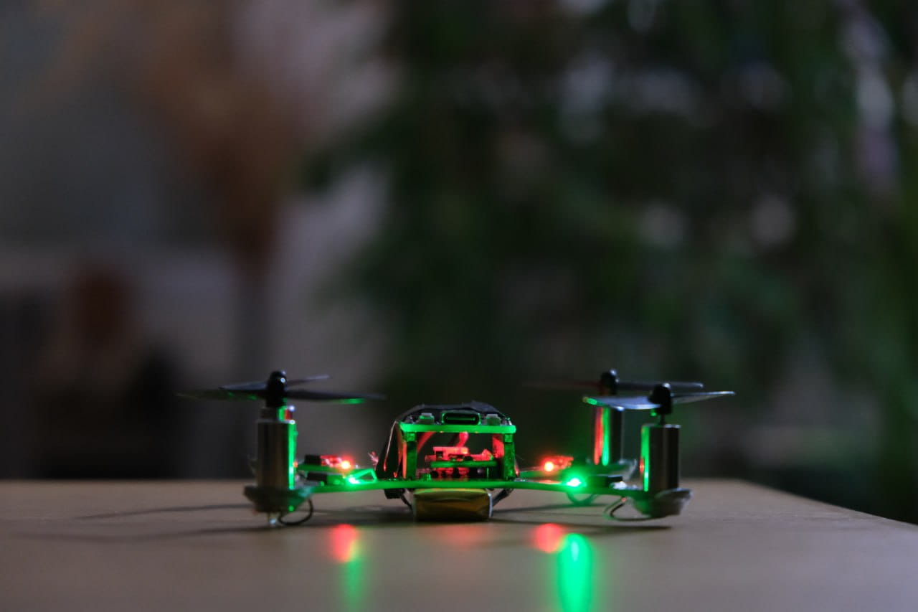
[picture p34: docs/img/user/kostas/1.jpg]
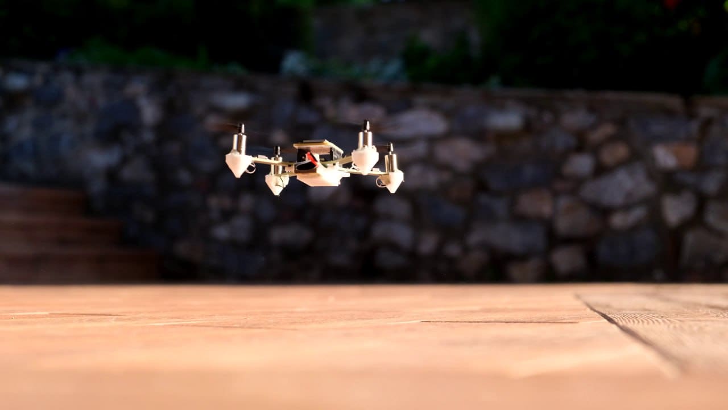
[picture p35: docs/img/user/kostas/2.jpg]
 

Detailed video about making the drone:



---

Author: [Awab Anas](http://t.me/AW_VENOM).<br>
Description: ESP32 D1 Mini, MPU-6050, 8520 3.7V brushed motors, 55 mm propellers, battery li-po 1200 mAh, controlling via [Mavlink Joystick app](https://github.com/goldarte/mavlink-joystick/releases/latest).<br>
[Flight validation](https://drive.google.com/file/d/12z0jfctZDBA6b5UKCG0Uje5rAxj6DhF-/view?usp=sharing).

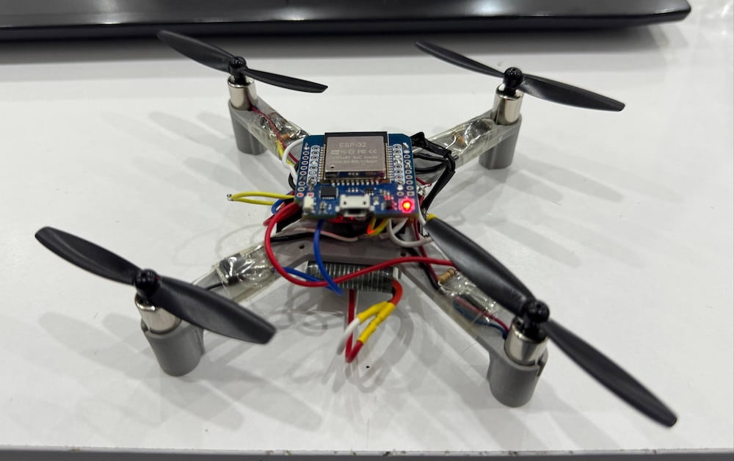
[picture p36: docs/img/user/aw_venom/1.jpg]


---

Author: [Ina Tix](https://t.me/ina_tix).<br>
Description: XR2981 based DC-DC converter, ELRS MINI 2.4GHz RX SX1280 receiver (SBUS interface), Radiomaster TX12 remote control.<br>
[Flight validation](https://drive.google.com/file/d/1yqkKNuz4R_yxGqUNQxVpixJbXqEEcUSj/view?usp=share_link).

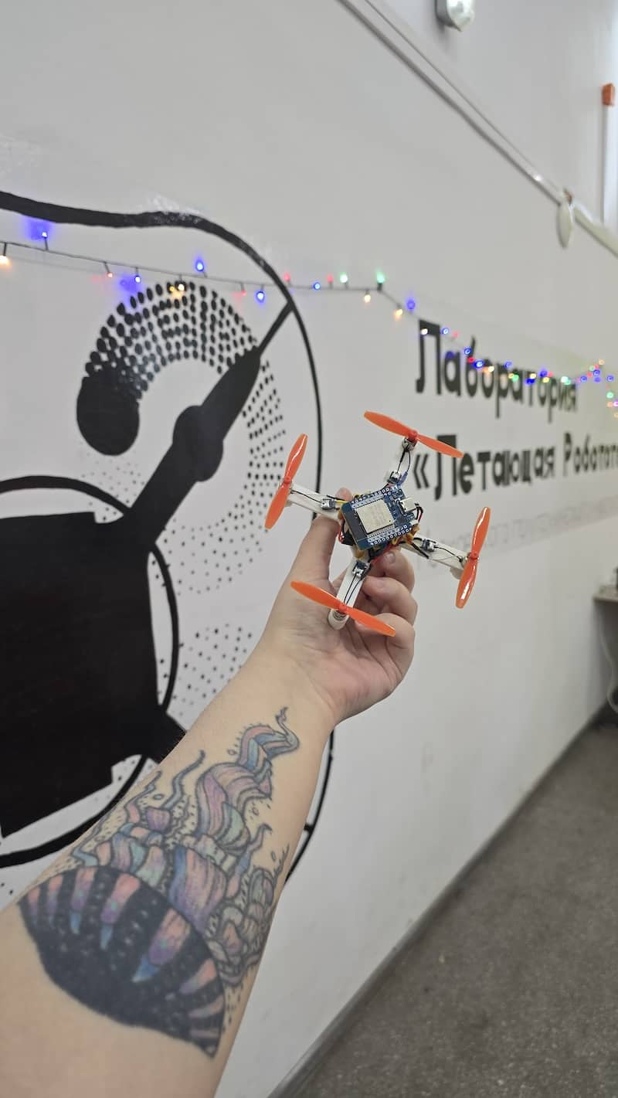
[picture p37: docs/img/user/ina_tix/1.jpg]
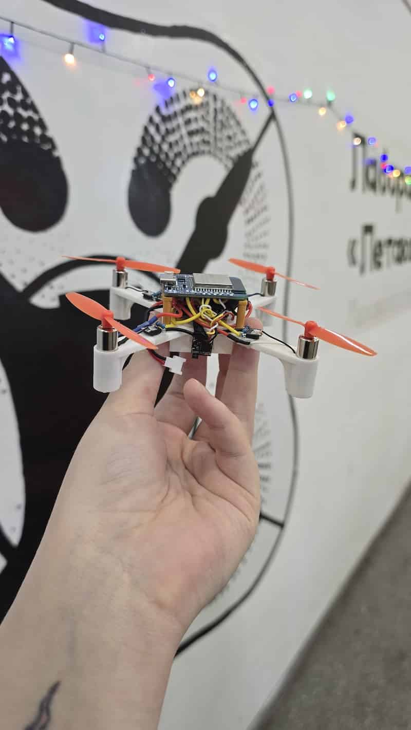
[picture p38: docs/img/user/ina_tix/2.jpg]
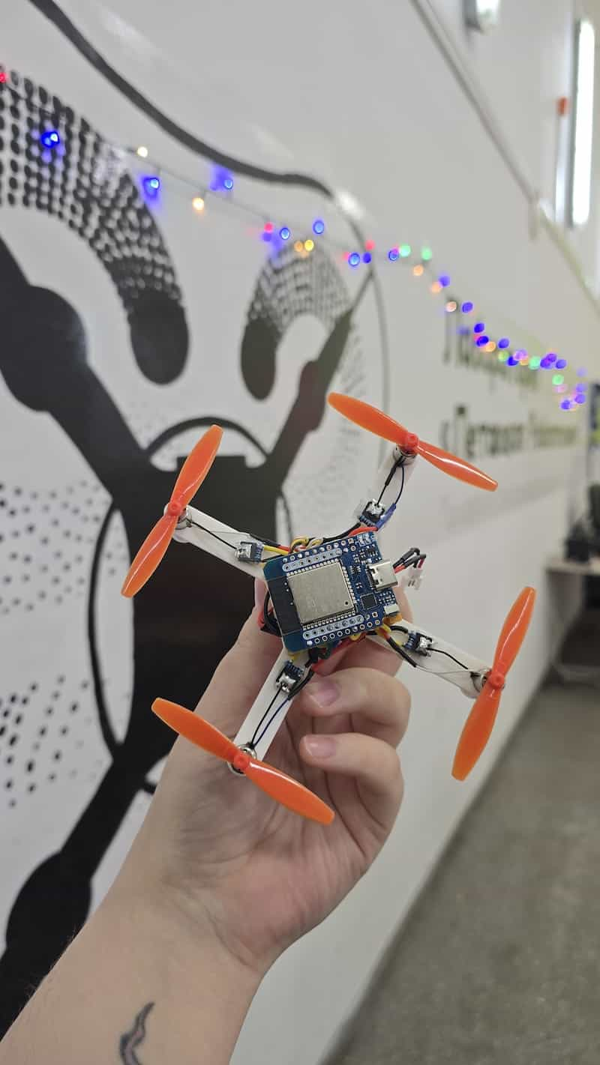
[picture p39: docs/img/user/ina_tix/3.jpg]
  

---

Author: Oleg Kalachev.<br>
Description: the first attempt on making an official PCB based Flix drone (Flix2 board). The IMU is not working on this version, so an external MPU-6050 board was used, therefore considered as **Flix version 1.5**.<br>
[Flight video](https://drive.google.com/file/d/1R7tuUsFmPY0CGcOCFfMFaCp9kR49K3bl/view?usp=sharing).

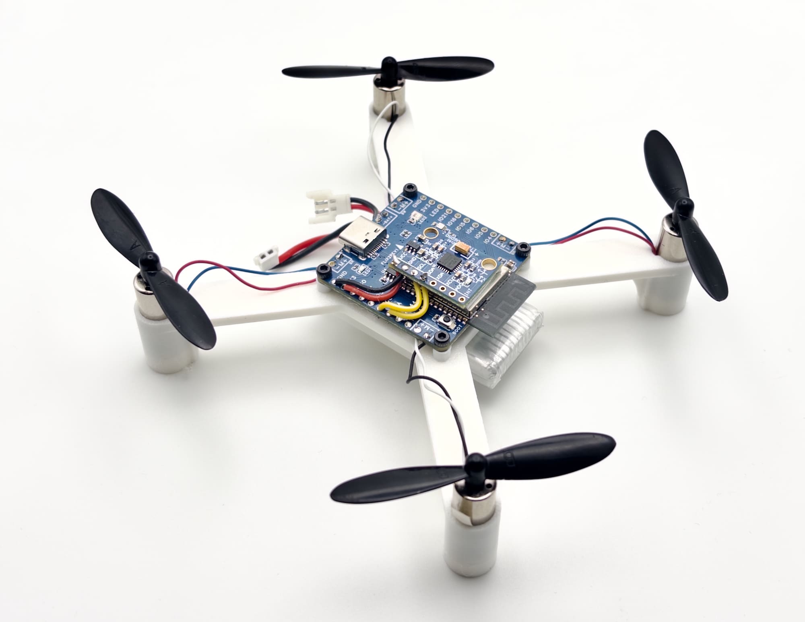
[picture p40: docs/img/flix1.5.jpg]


---

Author: [FanBy0ru](https://https://github.com/FanBy0ru).<br>
Description: custom 3D-printed frame.<br>
Frame STLs and flight validation: https://cults3d.com/en/3d-model/gadget/armature-pour-flix-drone.

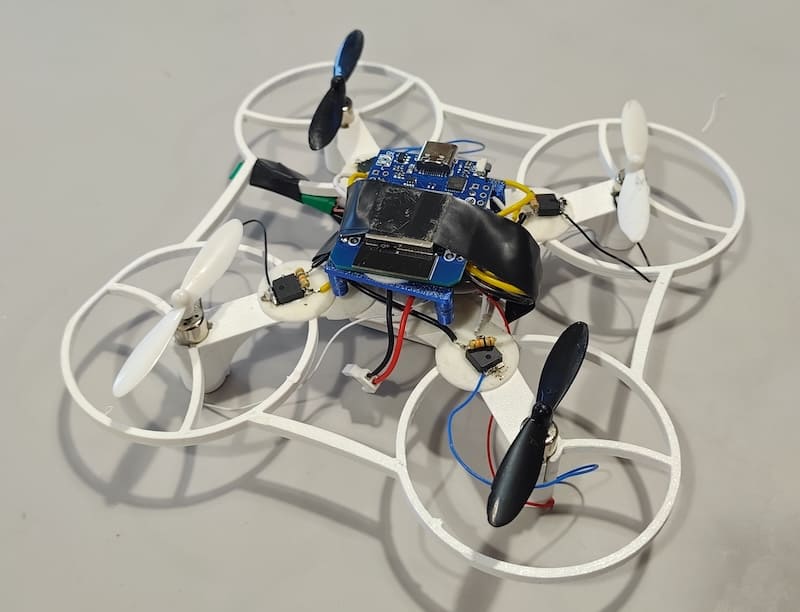
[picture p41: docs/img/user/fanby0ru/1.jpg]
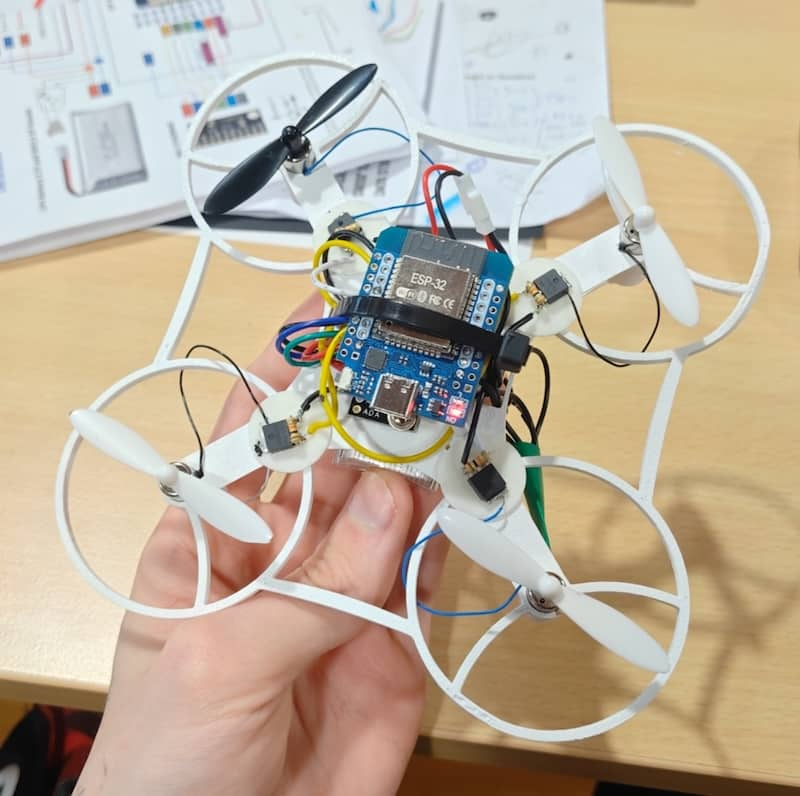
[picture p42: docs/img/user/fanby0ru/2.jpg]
 

---

Author: Ivan44 Phalko.<br>
Description: custom PCB, cusom test bench.<br>
[Flight validation](https://drive.google.com/file/d/17DNDJ1gPmCmDRAwjedCbJ9RXAyqMqqcX/view?usp=sharing).

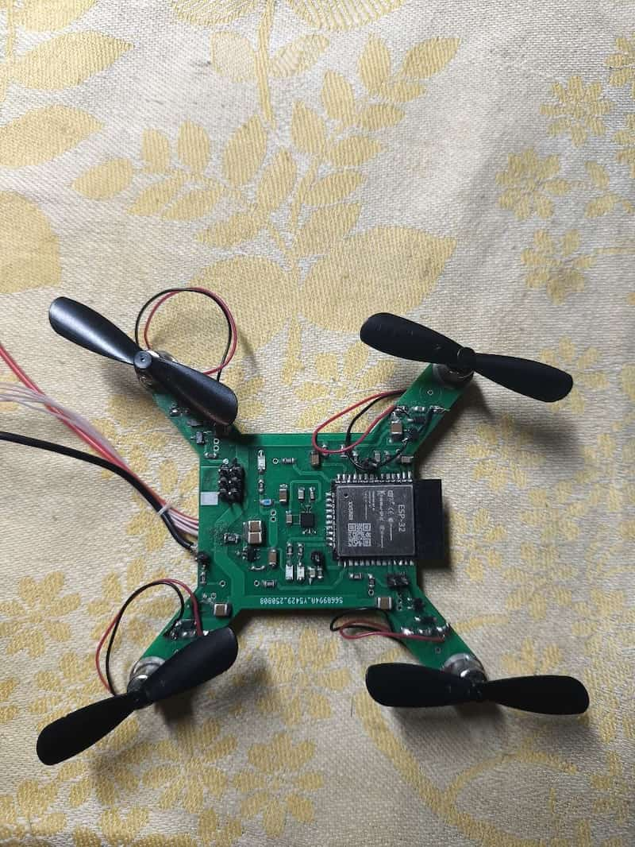
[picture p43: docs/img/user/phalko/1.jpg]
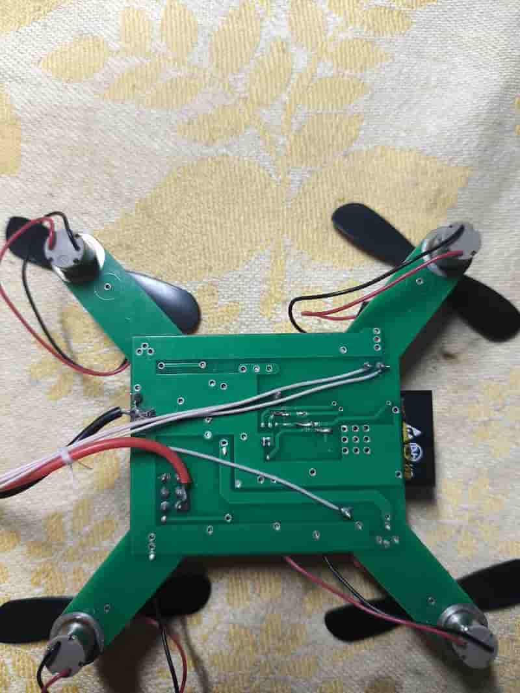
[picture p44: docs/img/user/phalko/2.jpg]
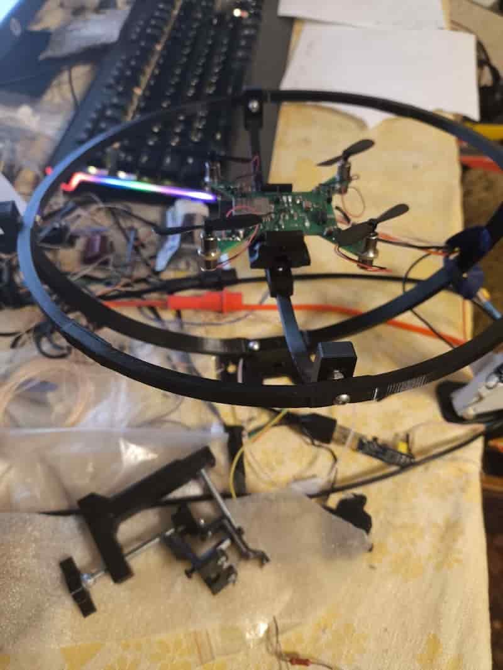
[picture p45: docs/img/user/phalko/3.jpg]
  

---

Author: **Arkadiy "Arky" Matsekh**, Foucault Dynamics, Gold Coast, Australia.<br>
The drone was built for the University of Queensland industry-led Master's capstone project.

**Flight video:**

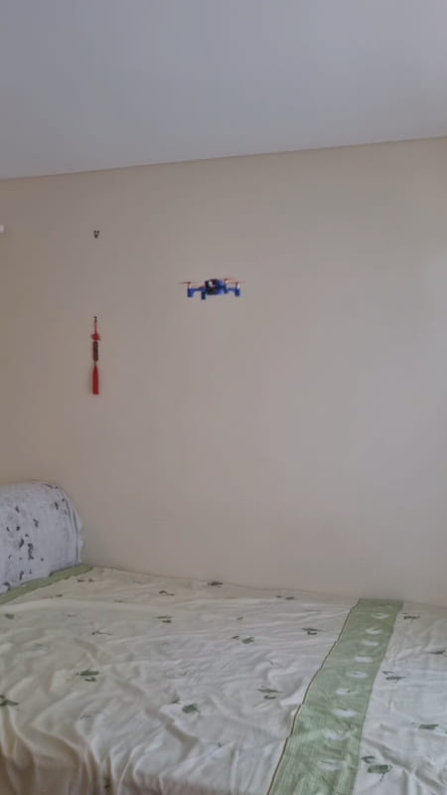
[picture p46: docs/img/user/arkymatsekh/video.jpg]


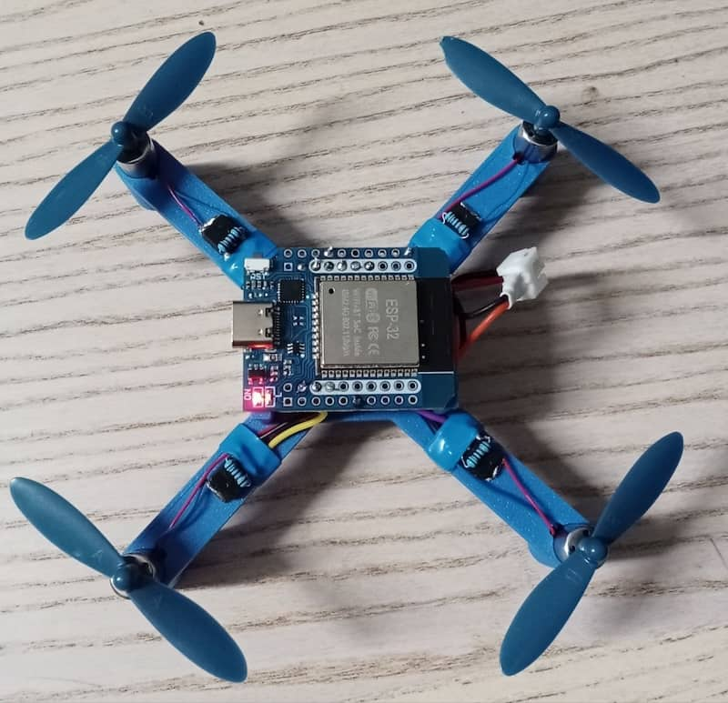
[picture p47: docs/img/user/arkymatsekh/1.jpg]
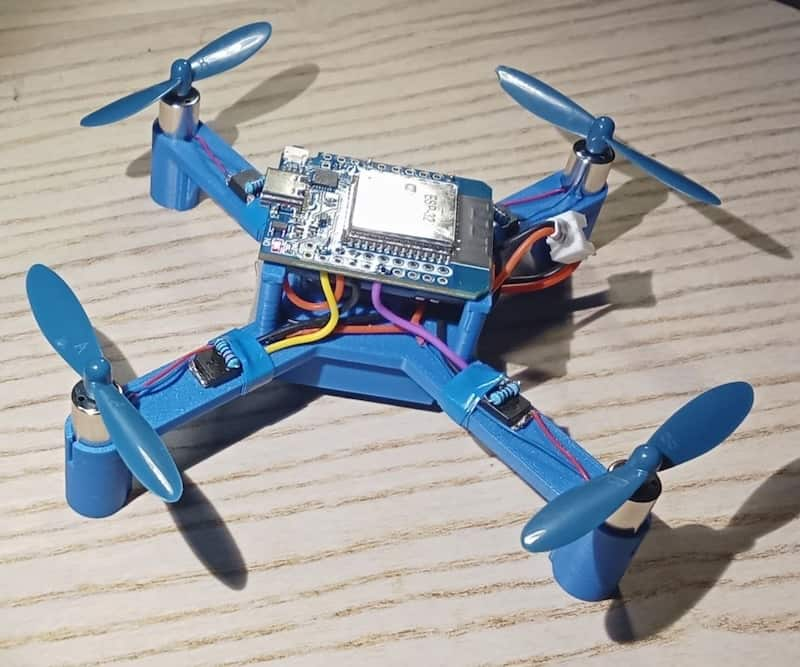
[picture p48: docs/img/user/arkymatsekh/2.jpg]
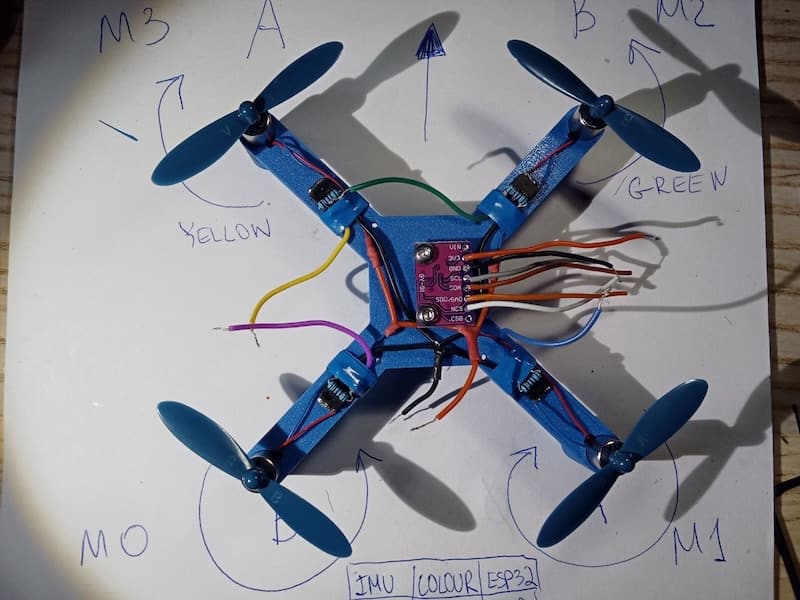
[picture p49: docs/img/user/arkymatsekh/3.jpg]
  

---

Author: [goldarte](https://t.me/goldarte).<br>

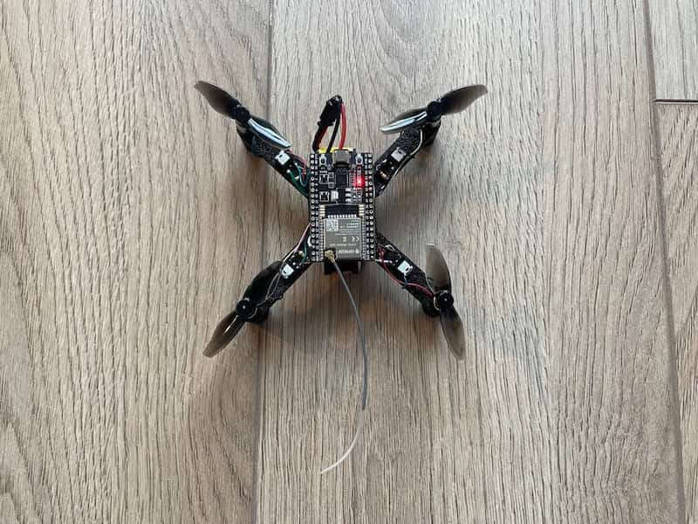
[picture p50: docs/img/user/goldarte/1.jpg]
 

**Flight video:**



---

Author: [malagis](https://oshwhub.com/malagis).<br>

A Chinese custom PCB version of Flix with a big community of users, lots of materials and modifications.

Main project's page: https://oshwhub.com/malagis/esp32-mini-plane.<br>
Video about the project: https://www.bilibili.com/video/BV14vyqBFEJn/.

  

---

## School 548 course

Special course on quadcopter design and engineering took place in october-november 2025 in School 548, Moscow. The course included UAV control theory, electronics, drone assembly and setup practice, using the Flix project.

  

STL files and other materials: see [here](https://drive.google.com/drive/folders/1wTUzj087LjKQQl3Lz5CjHCuobxoykhyp?usp=share_link).

### Selected works

Author: [KiraFlux](https://t.me/@kiraflux_0XC0000005).<br>
Description: **custom ESPNOW remote control** was implemented, modified firmware to support ESPNOW protocol.<br>
Telegram posts: [1](https://t.me/opensourcequadcopter/106), [2](https://t.me/opensourcequadcopter/114).<br>
Modified Flix firmware: https://github.com/KiraFlux/flix/tree/klyax.<br>
Remote control project: https://github.com/KiraFlux/ESP32-DJC.<br>
Drone design: https://github.com/KiraFlux/Klyax.<br>

 

**ESPNOW remote control demonstration**:



Author: [tolyan4krut](https://t.me/tolyan4krut).<br>
Description: the first drone based on ESP32-S3-CAM board **with a camera**, implementing Wi-Fi video streaming. Runs HTTP server and HTTP video stream.<br>
Modified Flix firmware: https://github.com/CatRey/Flix-Camera-Streaming.<br>
[Telegram post](https://t.me/opensourcequadcopter/117).



**Video streaming and flight demonstration**:



Author: [Vlad Tolshinov](https://t.me/Vlad_Tolshinov).<br>
Description: custom frame with enlarged arm length, which provides very high flight stability, 65 mm props.

 

**Flight video**:



---

## RoboCamp

Author: RoboCamp participants.<br>
Description: 3D-printed and wooden frames, ESP32 Mini, DC-DC buck-boost converters. BetaFPV LiteRadio 3 to control the drones via Wi-Fi connection.<br>
Features: altitude hold, obstacle avoidance, autonomous flight elements.<br>
Some of the designed model files: see [here](https://drive.google.com/drive/folders/18YHWGquKeIevzrMH4-OUT-zKXMETTEUu?usp=share_link).

RoboCamp took place in July 2025, Saint Petersburg, where 9 participants designed and built their own drones using the Flix project, and then modified the firmware to complete specific flight tasks.

See the detailed video about the event:



Built drones:



---

Author: chkroko.<br>
Description: the first Flix drone built with **brushless motors** (DShot interface).<br>
Features: SpeedyBee BLS 35A Mini V2 ESC, ESP32-S3 board, EMAX ECO 2 2207 1700kv motors, ICM20948V2 IMU, INA226 power monitor and Bluetooth gamepad for control.<br>
Patch for DShot ESC: https://github.com/Krokodilushka/flix/commit/568345a45ca7ed5b458a11a9d0a9f4c8a91e70ac.

**Flight video:**



  

---

Author: chkroko.<br>
Modification: Control using Bluetooth with **Flydigi Vader 3** gamepad. Source code: https://github.com/Krokodilushka/flix/tree/dev.<br>
Features: ESP32-C3 SuperMini, BMP580 barometer, INA226 power monitor, IRLZ44N MOSFETs.<br>
Full description: https://telegra.ph/Flix-dron-06-13.

**Flight video:**



 

---

Author: chkroko.<br>
Features: ESP32-C3 SuperMini board, INA226 power monitor, IRLZ44N MOSFETs, MPU-6500 IMU.

**Flight video:**



 

---

Author: [@jeka_chex](https://t.me/jeka_chex).<br>
Features: custom frame, FPV camera, 3-blade 31 mm propellers.<br>
Motor drivers: AON7410 MOSFET + capacitors.<br>
Custom frame files: https://drive.google.com/drive/folders/1QCIc-_YYFxJN4cMhVLjL5SflqegvCowm?usp=share_link.<br>

**Flight video:**



**FPV flight video:**



    

---

Author: [@fisheyeu](https://t.me/fisheyeu).<br>
[Video](https://drive.google.com/file/d/1IT4eMmWPZpmaZR_qsIRmNJ52hYkFB_0q/view?usp=share_link).

 

---

Author: [@p_kabakov](https://t.me/p_kabakov).<br>
Custom propellers guard 3D-model: https://drive.google.com/file/d/1TKnzwvrZYzYuRTLLERNmnKH71H9n4Xj_/view?usp=share_link.<br>
Features: ESP32-C3 microcontroller is used.<br>
[Video](https://drive.google.com/file/d/1B0NMcsk0fgwUgNr9XuLOdR2yYCuaj008/view?usp=share_link).

  

**Custom Wi-Fi RC control:**



See source and description (in Russian): https://github.com/pavelkabakov/flix/tree/master/rc_control_v1.

---

Author: [@yi_lun](https://t.me/yi_lun).<br>
[Video](https://drive.google.com/file/d/1TkSuvHQ_0qQPFUpY5XjJzmhnpX_07cTg/view?usp=share_link).

 

---

Author: [@peter_ukhov](https://t.me/peter_ukhov).<br>
Features: customized ESP32 holder, GY-ICM20948V2 IMU board, boost-converter for powering the ESP32.<br>
Files for 3D-printing: https://drive.google.com/file/d/1Sma-FEzFBj2HA5ixJtUyH0uWixvr6vdK/view?usp=share_link.<br>
Schematics: https://miro.com/app/board/uXjVN-dTjoo=/?moveToWidget=3458764612179508274&cot=14.<br>



 

---

Author: [@Alexey_Karakash](https://t.me/Alexey_Karakash).<br>
Files for 3D printing of the custom frame: https://drive.google.com/file/d/1tkNmujrHrKpTMVtsRH3mor2zdAM0JHum/view?usp=share_link.<br>



    

---

Author: [@rudpa](https://t.me/rudpa).<br>



  

---

Author: [@peter_ukhov](https://t.me/peter_ukhov).<br>
Schematics: https://miro.com/app/board/uXjVN-dTjoo=/?moveToWidget=3458764612338222067&cot=14.<br>





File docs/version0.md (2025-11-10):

# Flix version 0

Flix version 0 (obsolete):

Flix quadcopter

## Components list

|Type|Part|Image|Quantity|
|-|-|-|-|
|Microcontroller board|ESP32 Mini||1|
|IMU and barometer² board|GY-91 (or other MPU-9250 board)||1|
|Quadcopter frame|K100||1|
|Motor|8520 3.7V brushed motor (**shaft 0.8mm!**)||4|
|Propeller|Hubsan 55 mm||4|
|Motor ESC|2.7A 1S Dual Way Micro Brush ESC||4|
|RC transmitter|KINGKONG TINY X8||1|
|RC receiver|DF500 (SBUS)||1|
|~~SBUS inverter~~*|||~~1~~|
|Battery|3.7 Li-Po 850 MaH 60C|||
|Battery charger|||1|
|Wires, connectors, tape, ...||||

*\* — not needed as ESP32 supports [software pin inversion](https://github.com/bolderflight/sbus#inverted-serial).*

## Schematics

Flix schematics

You can also check a user contributed [variant of complete circuit diagram](https://miro.com/app/board/uXjVN-dTjoo=/?moveToWidget=3458764574482511443&cot=14) of the drone.

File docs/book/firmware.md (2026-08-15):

# Архитектура прошивки

Прошивка Flix это обычный скетч Arduino, реализованный в однопоточном стиле. Код инициализации находится в функции `setup()`, а главный цикл — в функции `loop()`. Скетч состоит из нескольких файлов, каждый из которых отвечает за определенную подсистему.

Firmware dataflow diagram

Главный цикл `loop()` работает на частоте 1000 Гц. Передача данных между подсистемами происходит через глобальные переменные:

* `t` *(float)* — текущее время шага, *с*.
* `dt` *(float)* — дельта времени между текущим и предыдущим шагами, *с*.
* `gyro` *(Vector)* — данные с гироскопа, *рад/с*.
* `acc` *(Vector)* — данные с акселерометра, *м/с<sup>2</sup>*.
* `rates` *(Vector)* — отфильтрованные угловые скорости, *рад/с*.
* `attitude` *(Quaternion)* — оценка ориентации (положения) дрона.
* `controlRoll`, `controlPitch`, `controlYaw`, `controlThrottle`, `controlMode` *(float)* — команды управления от пилота, в диапазоне [-1, 1].
* `motors` *(float[4])* — выходные сигналы на моторы, в диапазоне [0, 1].

## Исходные файлы

Исходные файлы прошивки находятся в директории `flix`. Основные файлы:

* [`flix.ino`](https://github.com/okalachev/flix/blob/master/flix/flix.ino) — основной файл Arduino-скетча. Определяет некоторые глобальные переменные и главный цикл.
* [`imu.ino`](https://github.com/okalachev/flix/blob/master/flix/imu.ino) — чтение данных с датчика IMU (гироскоп и акселерометр), калибровка IMU.
* [`rc.ino`](https://github.com/okalachev/flix/blob/master/flix/rc.ino) — чтение данных с RC-приемника, калибровка RC.
* [`estimate.ino`](https://github.com/okalachev/flix/blob/master/flix/estimate.ino) — оценка ориентации дрона, комплементарный фильтр.
* [`control.ino`](https://github.com/okalachev/flix/blob/master/flix/control.ino) — подсистема управления, трехмерный двухуровневый каскадный ПИД-регулятор.
* [`motors.ino`](https://github.com/okalachev/flix/blob/master/flix/motors.ino) — выход PWM на моторы.
* [`mavlink.ino`](https://github.com/okalachev/flix/blob/master/flix/mavlink.ino) — взаимодействие с QGroundControl или [pyflix](https://github.com/okalachev/flix/tree/master/tools/pyflix) через протокол MAVLink.

Вспомогательные файлы:

* [`vector.h`](https://github.com/okalachev/flix/blob/master/flix/vector.h), [`quaternion.h`](https://github.com/okalachev/flix/blob/master/flix/quaternion.h) — библиотеки векторов и кватернионов.
* [`pid.h`](https://github.com/okalachev/flix/blob/master/flix/pid.h) — ПИД-регулятор.
* [`filter.h`](https://github.com/okalachev/flix/blob/master/flix/filter.h) — фильтр нижних частот.

### Подсистема управления

Состояние органов управления обрабатывается в функции `interpretControls()` и преобразуется в **команду управления**, которая включает следующее:

* `attitudeTarget` *(Quaternion)* — целевая ориентация дрона.
* `ratesTarget` *(Vector)* — целевые угловые скорости, *рад/с*.
* `ratesExtra` *(Vector)* — дополнительные (feed-forward) угловые скорости, для управления рысканием в режиме STAB, *рад/с*.
* `torqueTarget` *(Vector)* — целевой крутящий момент, диапазон [-1, 1].
* `thrustTarget` *(float)* — целевая общая тяга, диапазон [0, 1].

Команда управления обрабатывается в функциях `controlAttitude()`, `controlRates()`, `controlTorque()`. Если значение одной из переменных установлено в `NAN`, то соответствующая функция пропускается.

Control subsystem diagram

Состояние *armed* хранится в переменной `armed`, а текущий режим — в переменной `mode`.

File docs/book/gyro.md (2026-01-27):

# Гироскоп

<div class="firmware">
	<strong>Файл прошивки:</strong>
	<a href="https://github.com/okalachev/flix/blob/canonical/flix/imu.ino"><code>imu.ino</code></a> <small>(каноничная версия)</small>.<br>
	Текущая версия: <a href="https://github.com/okalachev/flix/blob/master/flix/imu.ino"><code>imu.ino</code></a>.
</div>

Поддержание стабильного полета квадрокоптера невозможно без датчиков обратной связи. Важнейший из них — это **MEMS-гироскоп**. MEMS-гироскоп это микроэлектромеханический аналог классического механического гироскопа.

Механический гироскоп состоит из вращающегося диска, который сохраняет свою ориентацию в пространстве. Благодаря этому эффекту возможно определить ориентацию объекта в пространстве.

В MEMS-гироскопе нет вращающихся частей, и он помещается в крошечную микросхему. Он может измерять только текущую угловую скорость вращения объекта вокруг трех осей: X, Y и Z.

|Механический гироскоп|MEMS-гироскоп|
|-|-|
|Механический гироскоп|MEMS-гироскоп MPU-9250|

MEMS-гироскоп обычно интегрирован в инерциальный модуль (IMU), в котором также находятся акселерометр и магнитометр. Модуль IMU часто называют 9-осевым датчиком, потому что он измеряет:

* Угловую скорость вращения по трем осям (гироскоп).
* Ускорение по трем осям (акселерометр).
* Магнитное поле по трем осям (магнитометр).

Flix поддерживает следующие модели IMU:

* InvenSense MPU-9250.
* InvenSense MPU-6500.
* InvenSense ICM-20948.

> [!NOTE]
> MEMS-гироскоп измеряет угловую скорость вращения объекта.

## Интерфейс подключения

Большинство модулей IMU подключаются к микроконтроллеру через интерфейсы I²C и SPI. Оба этих интерфейса являются *шинами данных*, то есть позволяют подключить к одному микроконтроллеру несколько устройств.

**Интерфейс I²C** использует два провода для передачи данных и тактового сигнала. Выбор устройства для коммуникации происходит при помощи передачи адреса устройства на шину. Разные устройства имеют разные адреса, и микроконтроллер может последовательно общаться с несколькими устройствами.

**Интерфейс SPI** использует два провода для передачи данных, еще один для тактового сигнала и еще один для выбора устройства. При этом для каждого устройства на шине выделяется отдельный GPIO-пин для выбора. В разных реализациях этот пин называется CS/NCS (Chip Select) или SS (Slave Select). Когда CS-пин устройства активен (напряжение на нем низкое), устройство выбрано для общения.

В полетных контроллерах IMU обычно подключают через SPI, потому что он обеспечивает значительно бо́льшую скорость передачи данных и меньшую задержку. Подключение IMU через интерфейс I²C (например, в случае нехватки пинов микроконтроллера) возможно, но не рекомендуется.

Подключение IMU к микроконтроллеру ESP32 через интерфейс SPI выглядит так:

|Пин платы IMU|Пин ESP32|
|-|-|
|VCC/3V3|3V3|
|GND|GND|
|SCL|IO18|
|SDA *(MOSI)*|IO23|
|SAO/AD0 *(MISO)*|IO19|
|NCS|IO5|

Кроме того, многие IMU могут «будить» микроконтроллер при наличии новых данных. Для этого используется пин INT, который подключается к любому GPIO-пину микроконтроллера. При такой конфигурации можно использовать прерывания для обработки новых данных с IMU, вместо периодического опроса датчика. Это позволяет снизить нагрузку на микроконтроллер в сложных алгоритмах управления.

> [!WARNING]
> На некоторых платах IMU, например, на ICM-20948, отсутствует стабилизатор напряжения, поэтому их нельзя подключать к пину VIN ESP32, который подает напряжение 5 В. Допустимо питание только от пина 3V3.

## Работа с гироскопом

Для взаимодействия с IMU, включая работу с гироскопом, в Flix используется библиотека *FlixPeriph*. Библиотека устанавливается через менеджер библиотек Arduino IDE:



Чтобы работать с IMU, используется класс, соответствующий модели IMU: `MPU9250`, `MPU6500` или `ICM20948`. Классы для работы с разными IMU имеют единообразный интерфейс для основных операций, поэтому возможно легко переключаться между разными моделями IMU. Датчик MPU-6500 практически полностью совместим с MPU-9250, поэтому фактически класс `MPU9250` поддерживает обе модели.

## Ориентация осей гироскопа

Данные с гироскопа представляют собой угловую скорость вокруг трех осей: X, Y и Z. Ориентацию этих осей у IMU InvenSense можно легко определить по небольшой точке в углу чипа. Оси координат и направление вращения для измерений гироскопа обозначены на диаграмме:

Оси координат IMU

Расположение осей координат в популярных платах IMU:

|GY-91|MPU-92/65|ICM-20948|
|-|-|-|
|Оси координат платы GY-91|Оси координат платы MPU-9265|Оси координат платы ICM-20948|

Магнитометр IMU InvenSense обычно является отдельным устройством, интегрированным в чип, поэтому его оси координат могут отличаться. Библиотека FlixPeriph скрывает это различие и приводит данные с магнитометра к системе координат гироскопа и акселерометра.

## Чтение данных

Интерфейс библиотеки FlixPeriph соответствует стилю, принятому в Arduino. Для начала работы с IMU необходимо создать объект соответствующего класса и вызвать метод `begin()`. В конструктор класса передается интерфейс, по которому подключен IMU (SPI или I²C):

```cpp
#include <FlixPeriph.h>
#include <SPI.h>

MPU9250 imu(SPI);

void setup() {
	Serial.begin(115200);
	bool success = imu.begin();
	if (!success) {
		Serial.println("Failed to initialize the IMU");
	}
}
```

Для однократного считывания данных используется метод `read()`. Затем данные с гироскопа получаются при помощи метода `getGyro(x, y, z)`. Этот метод записывает в переменные `x`, `y` и `z` угловые скорости вокруг соответствующих осей в радианах в секунду.

Если нужно гарантировать, что будут считаны новые данные, можно использовать метод `waitForData()`. Этот метод блокирует выполнение программы до тех пор, пока в IMU не появятся новые данные. Метод `waitForData()` позволяет привязать частоту главного цикла `loop` к частоте обновления данных IMU. Это удобно для организации главного цикла управления квадрокоптером.

Программа для чтения данных с гироскопа и вывода их в консоль для построения графиков в Serial Plotter выглядит так:

```cpp
#include <FlixPeriph.h>
#include <SPI.h>

MPU9250 imu(SPI);

void setup() {
	Serial.begin(115200);
	bool success = imu.begin();
	if (!success) {
		Serial.println("Failed to initialize the IMU");
	}
}

void loop() {
	imu.waitForData();

	float gx, gy, gz;
	imu.getGyro(gx, gy, gz);

	Serial.printf("gx:%f gy:%f gz:%f\n", gx, gy, gz);
	delay(50); // замедление вывода
}
```

После запуска программы в Serial Plotter можно увидеть графики угловых скоростей. Например, при вращениях IMU вокруг вертикальной оси Z графики будут выглядеть так:



## Конфигурация гироскопа

В коде Flix настройка IMU происходит в функции `configureIMU`. В этой функции настраиваются три основных параметра гироскопа: диапазон измерений, частота сэмплирования и частота LPF-фильтра.

### Частота сэмплирования

Большинство IMU могут обновлять данные с разной частотой. В полетных контроллерах обычно используется частота обновления от 500 Гц до 8 кГц. Чем выше частота, тем выше точность управления полетом, но и тем больше нагрузка на микроконтроллер.

Частота сэмплирования устанавливается методом `setSampleRate()`. В Flix используется частота 1 кГц:

```cpp
IMU.setRate(IMU.RATE_1KHZ_APPROX);
```

Поскольку не все поддерживаемые IMU могут работать строго на частоте 1 кГц, в библиотеке FlixPeriph существует возможность приближенной настройки частоты сэмплирования. Например, у IMU ICM-20948 при такой настройке реальная частота сэмплирования будет равна 1125 Гц.

Другие доступные для установки в библиотеке FlixPeriph частоты сэмплирования:

* `RATE_MIN` — минимальная частота для конкретного IMU.
* `RATE_50HZ_APPROX` — значение, близкое к 50 Гц.
* `RATE_1KHZ_APPROX` — значение, близкое к 1 кГц.
* `RATE_8KHZ_APPROX` — значение, близкое к 8 кГц.
* `RATE_MAX` — максимальная частота для конкретного IMU.

#### Диапазон измерений

Большинство MEMS-гироскопов поддерживают несколько диапазонов измерений угловой скорости. Главное преимущество выбора меньшего диапазона — бо́льшая чувствительность. В полетных контроллерах обычно выбирается максимальный диапазон измерений от –2000 до 2000 градусов в секунду, чтобы обеспечить возможность быстрых маневров.

В библиотеке FlixPeriph диапазон измерений гироскопа устанавливается методом `setGyroRange()`:

```cpp
imu.setGyroRange(imu.GYRO_RANGE_2000DPS);
```

### LPF-фильтр

IMU InvenSense могут фильтровать измерения на аппаратном уровне при помощи фильтра нижних частот (LPF). Flix реализует собственный фильтр для гироскопа, чтобы иметь больше гибкости при поддержке разных IMU. Поэтому для встроенного LPF устанавливается максимальная частота среза:

```cpp
imu.setDLPF(imu.DLPF_MAX);
```

## Калибровка гироскопа

Как и любое измерительное устройство, гироскоп вносит искажения в измерения. Наиболее простая модель этих искажений делит их на статические смещения *(bias)* и случайный шум *(noise)*:

\\[ gyro_{xyz}=rates_{xyz}+bias_{xyz}+noise \\]

Для точной работы подсистемы оценки ориентации и управления дроном необходимо оценить *bias* гироскопа и учесть его в вычислениях. Для этого при запуске программы производится калибровка гироскопа, которая реализована в функции `calibrateGyro()`. Эта функция считывает данные с гироскопа в состоянии покоя 1000 раз и усредняет их. Полученные значения считаются *bias* гироскопа и в дальнейшем вычитаются из измерений.

Программа для вывода данных с гироскопа с калибровкой:

```cpp
#include <FlixPeriph.h>
#include <SPI.h>

MPU9250 imu(SPI);

float gyroBiasX, gyroBiasY, gyroBiasZ; // bias гироскопа

void setup() {
	Serial.begin(115200);
	bool success = imu.begin();
	if (!success) {
		Serial.println("Failed to initialize the IMU");
	}
	calibrateGyro();
}

void loop() {
	float gx, gy, gz;
	imu.waitForData();
	imu.getGyro(gx, gy, gz);

	// Устранение bias гироскопа
	gx -= gyroBiasX;
	gy -= gyroBiasY;
	gz -= gyroBiasZ;

	Serial.printf("gx:%f gy:%f gz:%f\n", gx, gy, gz);
	delay(50); // замедление вывода
}

void calibrateGyro() {
	const int samples = 1000;
	Serial.println("Calibrating gyro, stand still");

	gyroBiasX = 0;
	gyroBiasY = 0;
	gyroBiasZ = 0;

	// Получение 1000 измерений гироскопа
	for (int i = 0; i < samples; i++) {
		imu.waitForData();
		float gx, gy, gz;
		imu.getGyro(gx, gy, gz);
		gyroBiasX += gx;
		gyroBiasY += gy;
		gyroBiasZ += gz;
	}

	// Усреднение значений
	gyroBiasX = gyroBiasX / samples;
	gyroBiasY = gyroBiasY / samples;
	gyroBiasZ = gyroBiasZ / samples;

	Serial.printf("Gyro bias X: %f\n", gyroBiasX);
	Serial.printf("Gyro bias Y: %f\n", gyroBiasY);
	Serial.printf("Gyro bias Z: %f\n", gyroBiasZ);
}
```

График данных с гироскопа в состоянии покоя без калибровки. Можно увидеть статическую ошибку каждой из осей:



График данных с гироскопа в состоянии покоя после калибровки:



Откалиброванные данные с гироскопа вместе с данными с акселерометра поступают в *подсистему оценки состояния*.

## Дополнительные материалы

* [MPU-9250 datasheet](https://invensense.tdk.com/wp-content/uploads/2015/02/PS-MPU-9250A-01-v1.1.pdf).
* [MPU-6500 datasheet](https://invensense.tdk.com/wp-content/uploads/2020/06/PS-MPU-6500A-01-v1.3.pdf).
* [ICM-20948 datasheet](https://invensense.tdk.com/wp-content/uploads/2016/06/DS-000189-ICM-20948-v1.3.pdf).

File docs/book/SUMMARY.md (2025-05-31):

<!-- markdownlint-disable MD041 -->
<!-- markdownlint-disable MD042 -->

[Главная](./README.md)

* [Архитектура прошивки](firmware.md)

# Учебник

* [Основы]()
* [Светодиод]()
* [Моторы]()
* [Радиоуправление]()
* [Вектор, кватернион](geometry.md)
* [Гироскоп](gyro.md)
* [Акселерометр]()
* [Оценка состояния]()
* [PID-регулятор]()
* [Режим ACRO]()
* [Режим STAB]()
* [Wi-Fi]()
* [MAVLink]()
* [Симуляция]()

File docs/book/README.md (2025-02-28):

# Flix

> [!IMPORTANT]
> Flix — это проект по созданию открытого квадрокоптера на базе ESP32 с нуля и учебника по разработке полетных контроллеров.

Flix quadcopter

<p class="github">GitHub:&nbsp;<a href="https://github.com/okalachev/flix">github.com/okalachev/flix</a>.</p>

<p class="telegram">Telegram-канал:&nbsp;<a href="https://t.me/opensourcequadcopter">@opensourcequadcopter</a>.</p>

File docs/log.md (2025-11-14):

# Log analysis

Flix quadcopter uses RAM to store flight log data. The default log capacity is 10 seconds at 100 Hz. This configuration can be adjusted in the `log.ino` file.

To perform log analysis, you need to download the flight log. To to that, ensure you're connected to the drone using Wi-Fi and run the following command:

```bash
make log
```

Logs are stored in `tools/log/*.csv` files.

## Analysis

### PlotJuggler

The recommended tool for log analysis is PlotJuggler.



1. Install PlotJuggler using the [official instructions](https://github.com/facontidavide/PlotJuggler?tab=readme-ov-file#installation).

2. Run PlotJuggler and drag'n'drop the downloaded log file there. Choose `t` column to be used as X axis.

   You can open the most recent downloaded file using the command:

   ```bash
   make plot
   ```

   You can perform both log download and run PlotJuggler in one command:

   ```bash
   make log plot
   ```

### FlightPlot

FlightPlot is a powerful tool for analyzing logs in [ULog format](https://docs.px4.io/main/en/dev_log/ulog_file_format.html). This format is used in PX4 and ArduPilot flight software.



1. [Install FlightPlot](https://github.com/PX4/FlightPlot).
2. Flix repository contains a tool for converting CSV logs to ULog format. Build the tool using [the instructions](../tools/csv_to_ulog/README.md) and convert the log you want to analyze.
3. Run FlightPlot and drag'n'drop the converted ULog-file there.

### Foxglove Studio

Foxglove is a tool for visualizing and analyzing robotics data with very rich functionality. It can import various formats, but mainly focuses on its own format, called [MCAP](https://mcap.dev).



1. Install Foxglove Studio from the [official website](https://foxglove.dev/download).

2. Flix repository contains a tool for converting CSV logs to MCAP format. First, install its dependencies:

   ```bash
   cd tools
   pip install -r requirements.txt
   ```

3. Convert the log you want to analyze:

   ```bash
   csv_to_mcap.py log_file.csv
   ```

4. Open the log in Foxglove Studio using *Open local file* command.

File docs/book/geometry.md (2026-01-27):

# Вектор, кватернион

В алгоритме управления квадрокоптером широко применяются геометрические (и алгебраические) объекты, такие как **векторы** и **кватернионы**. Они позволяют упростить математические вычисления и улучшить читаемость кода. В этой главе мы рассмотрим именно те геометрические объекты, которые используются в алгоритме управления квадрокоптером Flix, причем акцент будет сделан на практических аспектах их использования.

## Система координат

### Оси координат

Для работы с объектами в трехмерном пространстве необходимо определить *систему координат*. Как известно, система координат задается тремя взаимно перпендикулярными осями, которые обозначаются как *X*, *Y* и *Z*. Порядок обозначения этих осей зависит от того, какую систему координат мы выбрали — *левую* или *правую*:

|Левая система координат|Правая система координат|
|---|---|
|Левая система координат|Правая система координат|

В Flix для всех математических расчетов используется **правая система координат**, что является стандартом в робототехнике и авиации.

Также необходимо выбрать направление осей — в Flix они выбраны в соответствии со стандартом [REP-103](https://www.ros.org/reps/rep-0103.html). Для величин, заданных в подвижной системе координат, связанной с корпусом дрона, применяется порядок <abbr title="Forward Left Up">FLU</abbr>:

* ось X — направлена **вперед**;
* ось Y — направлена **влево**;
* ось Z — направлена **вверх**.

Для величин, заданных в *мировой* системе координат (относительно фиксированной точки в пространстве) — <abbr title="East North Up">ENU</abbr>:

* ось X — направлена на **восток** (условный);
* ось Y — направлена на **север** (условный);
* ось Z — направлена **вверх**.

> [!NOTE]
> Для системы ENU важно только взаимное направление осей. Если доступен магнитометр, то используются реальные восток и север, но если нет — то произвольно выбранные.

Углы и угловые скорости определяются в соответствии с правилами математики: значения увеличиваются против часовой стрелки, если смотреть в сторону начала координат. Общий вид системы координат:

Система координат

> [!TIP]
> Оси координат <i>X</i>, <i>Y</i> и <i>Z</i> часто обозначаются красными, зелеными и синими цветами соответственно. Запомнить это можно с помощью сокращения <abbr title="Red Green Blue">RGB</abbr>.

## Вектор

<div class="firmware">
	<strong>Файл прошивки:</strong>
	<a href="https://github.com/okalachev/flix/blob/master/flix/vector.h"><code>vector.h</code></a>.<br>
</div>

**Вектор** — простой геометрический объект, который содержит три значения, соответствующие координатам *X*, *Y* и *Z*. Эти значения называются *компонентами вектора*. Вектор может описывать точку в пространстве, направление или ось вращения, скорость, ускорение, угловые скорости и другие физические величины. В Flix векторы задаются объектами `Vector` из библиотеки `vector.h`:

```cpp
Vector v(1, 2, 3);
v.x = 5;
v.y = 10;
v.z = 15;
```

> [!TIP]
> Не следует путать геометрический вектор — <code>vector</code> и динамический массив в стандартной библиотеке C++ — <code>std::vector</code>.

В прошивке в виде векторов представлены, например:

* `acc` собственное ускорение с акселерометра.
* `gyro` — угловые скорости с гироскопа.
* `rates` — рассчитанная угловая скорость дрона.
* `accBias`, `accScale`, `gyroBias` — параметры калибровки IMU.

### Операции с векторами

**Длина вектора** рассчитывается при помощи теоремы Пифагора; в прошивке используется метод `norm()`:

```cpp
Vector v(3, 4, 5);
float length = v.norm(); // 7.071
```

Любой вектор можно привести к **единичному вектору** (сохранить направление, но сделать длину равной 1) при помощи метода `normalize()`:

```cpp
Vector v(3, 4, 5);
v.normalize(); // 0.424, 0.566, 0.707
```

**Сложение и вычитание** векторов реализуется через простое покомпонентное сложение и вычитание. Геометрически сумма векторов представляет собой вектор, который соединяет начало первого вектора с концом второго. Разность векторов представляет собой вектор, который соединяет конец первого вектора с концом второго. Это удобно для расчета относительных позиций, суммарных скоростей и решения других задач. В коде эти операции интуитивно понятны:

```cpp
Vector a(1, 2, 3);
Vector b(4, 5, 6);
Vector sum = a + b; // 5, 7, 9
Vector diff = a - b; // -3, -3, -3
```

Операция **умножения на число** `n` увеличивает (или уменьшает) длину вектора в `n` раз (сохраняя направление):

```cpp
Vector a(1, 2, 3);
Vector b = a * 2; // 2, 4, 6
```

В некоторых случаях полезна операция **покомпонентного умножения** (или деления) векторов. Например, для применения коэффициентов калибровки к данным с IMU. В разных библиотеках эта операция обозначается по разному, но в библиотеке `vector.h` используется простые знаки `*` и `/`:

```cpp
acc = acc / accScale;
```

**Угол между векторами** можно найти при помощи статического метода `Vector::angleBetween()`:

```cpp
Vector a(1, 0, 0);
Vector b(0, 1, 0);
float angle = Vector::angleBetween(a, b); // 1.57 (90 градусов)
```

#### Скалярное произведение

Скалярное произведение векторов *(dot product)* — это произведение длин двух векторов на косинус угла между ними. В математике оно обозначается знаком `·` или слитным написанием векторов. Интуитивно, результат скалярного произведения показывает, насколько два вектора *сонаправлены*.

В Flix используется статический метод `Vector::dot()`:

```cpp
Vector a(1, 2, 3);
Vector b(4, 5, 6);
float dotProduct = Vector::dot(a, b); // 32
```

Операция скалярного произведения может помочь, например, при расчете проекции одного вектора на другой.

#### Векторное произведение

Векторное произведение *(cross product)* позволяет найти вектор, перпендикулярный двум другим векторам. В математике оно обозначается знаком `×`, а в прошивке используется статический метод `Vector::cross()`:

```cpp
Vector a(1, 2, 3);
Vector b(4, 5, 6);
Vector crossProduct = Vector::cross(a, b); // -3, 6, -3
```

## Кватернион

### Ориентация в трехмерном пространстве

В отличие от позиции и скорости, у ориентации в трехмерном пространстве нет универсального для всех случаев способа представления. В зависимости от задачи ориентация может быть представлена в виде *углов Эйлера*, *матрицы поворота*, *вектора вращения* или *кватерниона*. Рассмотрим используемые в полетной прошивке способы представления ориентации.

### Углы Эйлера

**Углы Эйлера** — *крен*, *тангаж* и *рыскание* — это наиболее «естественный» для человека способ представления ориентации. Они описывают последовательные вращения объекта вокруг трех осей координат.

В прошивке углы Эйлера сохраняются в обычный объект `Vector` (хоть и, строго говоря, не являются вектором):

* Угол по крену *(roll)* — `vector.x`.
* Угол по тангажу *(pitch)* — `vector.y`.
* Угол по рысканию *(yaw)* — `vector.z`.

Особенности углов Эйлера:

1. Углы Эйлера зависят от порядка применения вращений, то есть существует 6 типов углов Эйлера. Порядок вращений, принятый в Flix (и в роботехнике в целом) — рыскание, тангаж, крен (ZYX).
2. Для некоторых ориентаций углы Эйлера «вырождаются». Так, если объект «смотрит» строго вниз, то угол по рысканию и угол по крену становятся неразличимыми. Эта ситуация называется *gimbal lock* — потеря одной степени свободы.

Ввиду этих особенности для углов Эйлера не существует общих формул для самых базовых задач с ориентациями, таких как применение одного вращения (ориентации) к другому, расчет разницы между ориентациями и подобных. Поэтому в основном углы Эйлера применяются в пользовательском интерфейсе, но редко используются в математических расчетах.

> [!IMPORTANT]
> Для углов Эйлера не существует общих формул для самых базовых операций с ориентациями.

### Axis-angle

Помимо углов Эйлера, любую ориентацию в трехмерном пространстве можно представить в виде вращения вокруг некоторой оси на некоторый угол. В геометрии это доказывается, как **теорема вращения Эйлера**. В таком представлении ориентация задается двумя величинами:

* **Ось вращения** *(axis)* — единичный вектор, определяющий ось вращения.
* **Угол поворота** *(angle* или *θ)* — угол, на который нужно повернуть объект вокруг этой оси.

В Flix ось вращения задается объектом `Vector`, а угол поворота — числом типа `float` в радианах:

```cpp
// Вращение на 45 градусов вокруг оси (1, 2, 3)
Vector axis(1, 2, 3);
float angle = radians(45);
```

Этот способ более удобен для расчетов, чем углы Эйлера, но все еще не является оптимальным.

### Вектор вращения

Если умножить вектор *axis* на угол поворота *θ*, то получится **вектор вращения** *(rotation vector)*. Этот вектор играет важную роль в алгоритмах управления ориентацией летательного аппарата.

Вектор вращения обладает замечательным свойством: если угловые скорости объекта (в собственной системе координат) в каждый момент времени совпадают с компонентами этого вектора, то за единичное время объект придет к заданной этим вектором ориентации. Это свойство позволяет использовать вектор вращения для управления ориентацией объекта посредством управления угловыми скоростями.

> [!IMPORTANT]
> Чтобы за единичное время прийти к заданной ориентации, собственные угловые скорости объекта должны быть равны компонентам вектора вращения.

Вектора вращения в Flix представляются в виде объектов `Vector`:

```cpp
// Вращение на 45 градусов вокруг оси (1, 2, 3)
Vector rotation = radians(45) * Vector(1, 2, 3);
```

### Кватернион

<div class="firmware">
	<strong>Файл прошивки:</strong>
	<a href="https://github.com/okalachev/flix/blob/master/flix/quaternion.h"><code>quaternion.h</code></a>.<br>
</div>

Вектор вращения удобен, но еще удобнее использовать **кватернион**. В Flix кватернионы задаются объектами `Quaternion` из библиотеки `quaternion.h`. Кватернион состоит из четырех значений: *w*, *x*, *y*, *z* и рассчитывается из вектора оси вращения *(axis)* и угла поворота *(θ)* по формуле:

\\[ q = \left( \begin{array}{c} w \\\\ x \\\\ y \\\\ z \end{array} \right) = \left( \begin{array}{c} \cos\left(\frac{\theta}{2}\right) \\\\ axis\_x \cdot \sin\left(\frac{\theta}{2}\right) \\\\ axis\_y \cdot \sin\left(\frac{\theta}{2}\right) \\\\ axis\_z \cdot \sin\left(\frac{\theta}{2}\right) \end{array} \right) \\]

На практике оказывается, что **именно такое представление наиболее удобно для математических расчетов**.

Проиллюстрируем кватернион и описанные выше способы представления ориентации на интерактивной визуализации. Изменяйте угол поворота *θ* с помощью ползунка (ось вращения константна) и изучите, как меняется ориентация объекта, вектор вращения и кватернион:

<div id="rotation-diagram" class="diagram">
	<p>
		<label class="angle" for="angle-range"></label>
		<input type="range" name="angle" id="angle-range" min="0" max="360" value="0" step="1">
	</p>

</div>

<script type="importmap">
{
	"imports": {
		"three": "https://cdn.jsdelivr.net/npm/three@0.176.0/build/three.module.js",
		"three/addons/": "https://cdn.jsdelivr.net/npm/three@0.176.0/examples/jsm/"
	}
}
</script>
<script type="module" src="js/rotation.js"></script>

> [!IMPORTANT]
> В контексте управляющих алгоритмов кватернион — это оптимизированный для расчетов аналог вектора вращения.

Кватернион это наиболее часто используемый способ представления ориентации в алгоритмах. Кроме этого, у кватерниона есть большое значение в теории чисел и алгебре, как у расширения понятия комплексного числа, но рассмотрение этого аспекта выходит за рамки описания работы с вращениями с практической точки зрения.

В прошивке в виде кватернионов представлены, например:

* `attitude` — текущая ориентация квадрокоптера.
* `attitudeTarget` — целевая ориентация квадрокоптера.

### Операции с кватернионами

Кватернион создается напрямую из четырех его компонент:

```cpp
// Кватернион, представляющий нулевую (исходную) ориентацию
Quaternion q(1, 0, 0, 0);
```

Кватернион можно создать из оси вращения и угла поворота, вектора вращения или углов Эйлера:

```cpp
Quaternion q1 = Quaternion::fromAxisAngle(axis, angle);
Quaternion q2 = Quaternion::fromRotationVector(rotation);
Quaternion q3 = Quaternion::fromEuler(Vector(roll, pitch, yaw));
```

И наоборот:

```cpp
q1.toAxisAngle(axis, angle);
Vector rotation = q2.toRotationVector();
Vector euler = q3.toEuler();
```

Возможно рассчитать вращение между двумя обычными векторами:

```cpp
Quaternion q = Quaternion::fromBetweenVectors(v1, v2); // в виде кватерниона
Vector rotation = Vector::rotationVectorBetween(v1, v2); // в виде вектора вращения
```

Шорткаты для работы с углом Эйлера по рысканью (удобно для алгоритмов управления полетом):

```cpp
float yaw = q.getYaw();
q.setYaw(yaw);
```

#### Применения вращений

Чтобы применить вращение, выраженное в кватернионе, к другому кватерниону, в математике используется операция **умножения кватернионов**. При использовании этой операции, необходимо учитывать, что она не является коммутативной, то есть порядок операндов имеет значение. Формула умножения кватернионов выглядит так:

\\[ q_1 \times q_2 = \left( \begin{array}{c} w_1 \\\\ x_1 \\\\ y_1 \\\\ z_1 \end{array} \right) \times \left( \begin{array}{c} w_2 \\\\ x_2 \\\\ y_2 \\\\ z_2 \end{array} \right) = \left( \begin{array}{c} w_1 w_2 - x_1 x_2 - y_1 y_2 - z_1 z_2 \\\\ w_1 x_2 + x_1 w_2 + y_1 z_2 - z_1 y_2 \\\\ w_1 y_2 - x_1 z_2 + y_1 w_2 + z_1 x_2 \\\\ w_1 z_2 + x_1 y_2 - y_1 x_2 + z_1 w_2 \end{array} \right) \\]

В библиотеке `quaternion.h` для этой операции используется статический метод `Quaternion::rotate()`:

```cpp
// Композиция вращений q1 и q2
Quaternion result = Quaternion::rotate(q1, q2);
```

Также полезной является операция применения вращения к вектору, которая делается похожим образом:

```cpp
// Вращение вектора v кватернионом q
Vector result = Quaternion::rotateVector(v, q);
```

Для расчета разницы между двумя ориентациями используется метод `Quaternion::between()`:

```cpp
// Расчет вращения от q1 к q2
Quaternion q = Quaternion::between(q1, q2);
```

## Дополнительные материалы

* [Интерактивный учебник по кватернионам](https://eater.net/quaternions).
* [Визуализация вращения вектора с помощью кватернионов](https://quaternions.online).

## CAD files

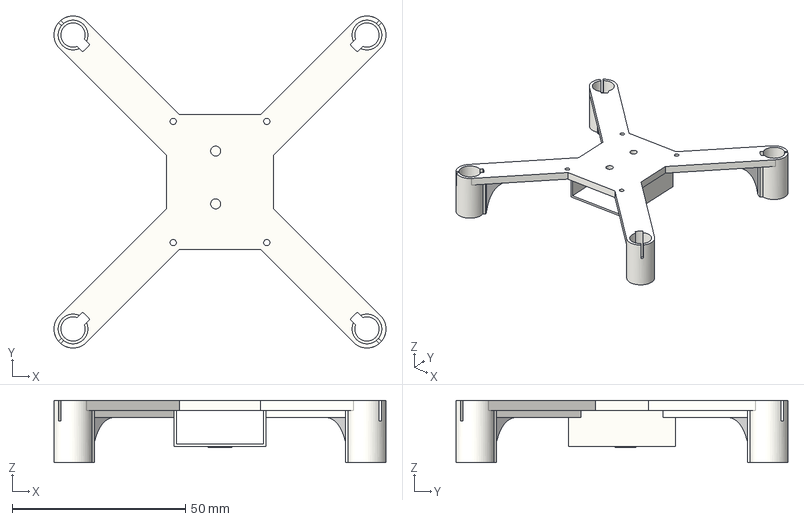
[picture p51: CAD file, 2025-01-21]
docs/assets/flix-frame-1.1.step
95.8 x 95.8 x 18.0 mm

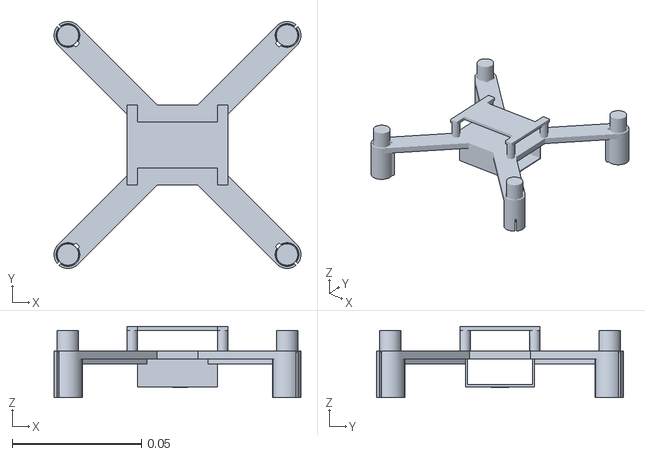
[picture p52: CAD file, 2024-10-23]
gazebo/models/flix/flix.stl
0.0957 x 0.0957 x 0.0276

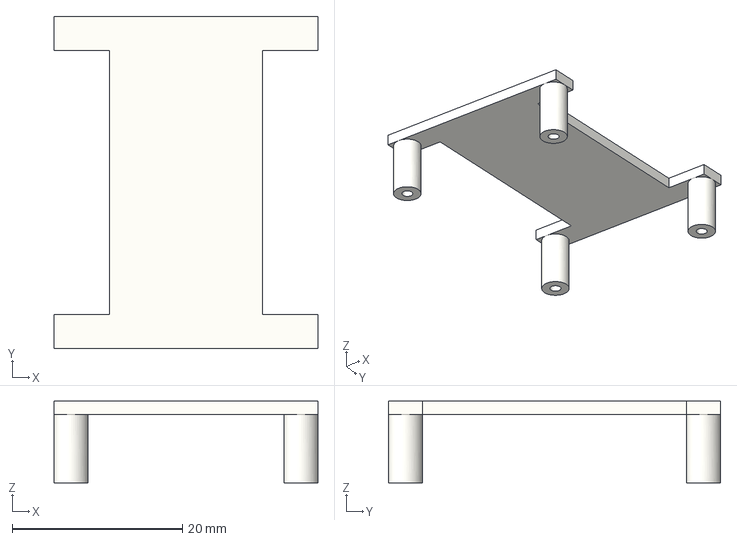
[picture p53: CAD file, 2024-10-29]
docs/assets/esp32-holder.step
31.0 x 39.0 x 9.60 mm

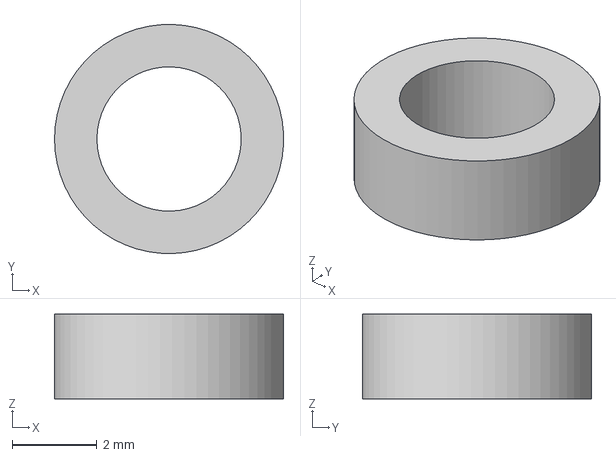
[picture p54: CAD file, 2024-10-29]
docs/assets/washer-m3.step
5.40 x 5.40 x 2.00 mm

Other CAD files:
docs/assets/flix-frame.step
docs/assets/esp32-holder.stl
docs/assets/flix-frame-1.1.stl
docs/assets/flix-frame.stl
docs/assets/washer-m3.stl

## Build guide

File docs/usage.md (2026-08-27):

# Usage: build, setup and flight

To fly Flix quadcopter, you need to upload the firmware to the ESP32 board, and set up the drone for flight.

## Uploading the firmware

You can either use the **prebuilt binaries** or **build the firmware** from sources — this will let you modify the firmware and add new features.

### Prebuilt binaries (the easiest way)

1. Download the latest firmware file using the following links:

   <!-- markdownlint-disable MD044 -->
   |Type|Boards|Link|
   |-|-|-|
   |ESP32|DevKit, D1 Mini|[`quadcopter.dev/flix.esp32.merged.bin`](https://quadcopter.dev/flix.esp32.merged.bin)|
   |ESP32-S3|Most S3 based|[`quadcopter.dev/flix.esp32s3.merged.bin`](https://quadcopter.dev/flix.esp32s3.merged.bin)|
   |ESP32-S3 (2MB PSRAM)|S3 Super Mini, S3 Zero (2MB PSRAM)|[`quadcopter.dev/flix.esp32s3.qspi.merged.bin`](https://quadcopter.dev/flix.esp32s3.qspi.merged.bin)|
   |ESP32-S3 (8/16MB PSRAM)|S3 Zero (8MB PSRAM)|[`quadcopter.dev/flix.esp32s3.opi.merged.bin`](https://quadcopter.dev/flix.esp32s3.opi.merged.bin)|
   |ESP32-C3|C3 Super Mini|[`quadcopter.dev/flix.esp32c3.merged.bin`](https://quadcopter.dev/flix.esp32c3.merged.bin)|
   |Flix2|Flix2 board|[`quadcopter.dev/flix.flix2.merged.bin`](https://quadcopter.dev/flix.flix2.merged.bin)|
   <!-- markdownlint-enable MD044 -->

2. Flash your ESP32 board using [ESP32 Web Flasher](https://www.espboards.dev/tools/program/):

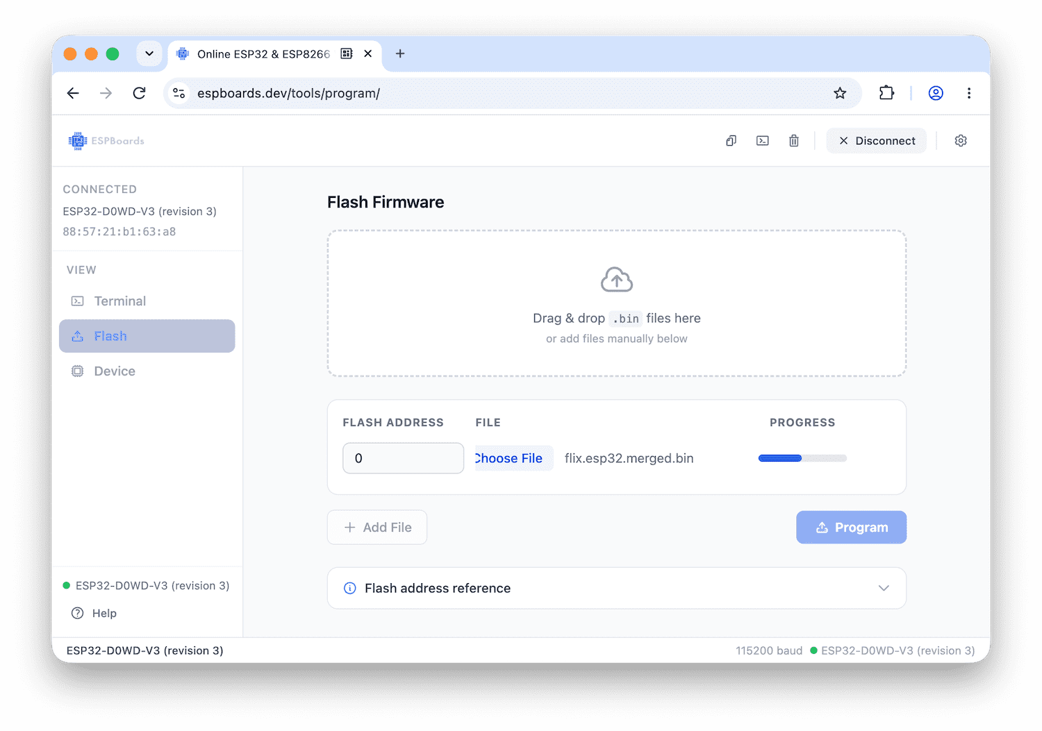
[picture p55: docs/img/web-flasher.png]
   

   * Connect the board to your computer, press *Connect to ESP*, choose the serial port.
   * Go to the *Flash* tab.
   * Choose the downloaded firmware file, set *Flash address* to *0* (important).
   * Click *Program* button and wait until the process is finished.

### Building from sources (flexible)

You can build and upload the firmware using either **Arduino IDE** (easier for beginners) or **command line**.

Get the sources using git:

```bash
git clone https://github.com/okalachev/flix.git && cd flix
```

Beginners can [download the sources as a ZIP archive](https://github.com/okalachev/flix/archive/refs/heads/master.zip).

#### Arduino IDE (Windows, Linux, macOS)

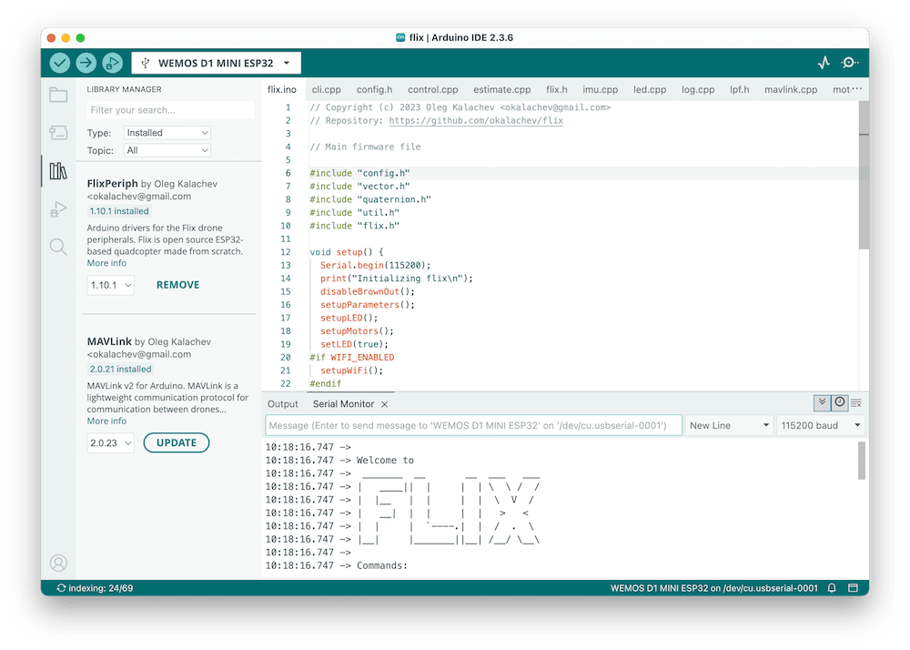
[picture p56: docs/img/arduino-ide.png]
Flix firmware open in Arduino IDE


1. Install [Arduino IDE](https://www.arduino.cc/en/software) (version 2 is recommended).
2. *Windows users might need to install [USB to UART bridge driver from Silicon Labs](https://www.silabs.com/developers/usb-to-uart-bridge-vcp-drivers).*
3. Install ESP32 core, version 3.3.10. See the [official Espressif's instructions](https://docs.espressif.com/projects/arduino-esp32/en/latest/installing.html#installing-using-arduino-ide) on installing ESP32 Core in Arduino IDE.
4. Install the following libraries using [Library Manager](https://docs.arduino.cc/software/ide-v2/tutorials/ide-v2-installing-a-library):
   * `FlixPeriph`, the latest version.
   * `MAVLink`, version 2.0.33.
5. Open the `flix/flix.ino` sketch from downloaded firmware sources in Arduino IDE.
6. Connect your ESP32 board to the computer and choose correct board type in Arduino IDE (*WEMOS D1 MINI ESP32* for ESP32 Mini, *ESP32S3 Dev Module* for ESP32-S3 Super Mini) and the port.
7. Set *Tools* ⇒ *Core Debug Level* to *Error* to see the errors in the serial console.
8. [Build and upload](https://docs.arduino.cc/software/ide-v2/tutorials/getting-started/ide-v2-uploading-a-sketch) the firmware using Arduino IDE.

#### Command line (Windows, Linux, macOS)

1. [Install Arduino CLI](https://arduino.github.io/arduino-cli/installation/).

   On Linux, install it like this:

   ```bash
   curl -fsSL https://raw.githubusercontent.com/arduino/arduino-cli/master/install.sh | BINDIR=~/.local/bin sh
   ```

2. Windows users might need to install [USB to UART bridge driver from Silicon Labs](https://www.silabs.com/developers/usb-to-uart-bridge-vcp-drivers).
3. Compile the firmware using `make`. Arduino dependencies will be installed automatically:

   ```bash
   make
   ```

   You can flash the firmware to the board using command:

   ```bash
   make upload
   ```

   You can also compile the firmware, upload it and start serial port monitoring using command:

   ```bash
   make upload monitor
   ```

   For ESP32-S3/ESP32-C3 boards, set the appropriate [FQBN](https://docs.arduino.cc/arduino-cli/FAQ/#whats-the-fqbn-string) using `BOARD` parameter:

   ```bash
   make BOARD=esp32:esp32:esp32s3 upload
   ```

See other available Make commands in [Makefile](../Makefile).

> [!TIP]
> You can test the firmware on a bare ESP32 board without connecting IMU and other peripherals. The Wi-Fi network `flix` should appear and all the basic functionality including console and QGroundControl connection should work.

## Before first flight

### Connect using QGroundControl

QGroundControl is a ground control station software that can be used to monitor and control the drone.

1. Install mobile or desktop version of [QGroundControl](https://docs.qgroundcontrol.com/master/en/qgc-user-guide/getting_started/download_and_install.html).
2. Power up the drone.
3. Connect your computer or smartphone to the appeared `flix` Wi-Fi network (password: `flixwifi`).
4. Launch QGroundControl app. It should connect and begin showing the drone's telemetry automatically.

> [!TIP]
> If QGroundControl doesn't connect, try to disable the firewall and/or VPN on your computer, as they may block the connection.

### Access console

The console is a command line interface (CLI) that allows to interact with the drone, change parameters, and perform various actions. There are two ways of accessing the console: using **serial port** or using **QGroundControl (wirelessly)**.

To access the console using serial port:

1. Connect the ESP32 board to the computer using USB cable.
2. Open Serial Monitor in Arduino IDE (or use `make monitor` in the command line).
3. In Arduino IDE, make sure the baudrate is set to 115200.

To access the console using QGroundControl:

1. Connect to the drone using QGroundControl app.
2. Go to the QGroundControl menu ⇒ *Analyze Tools* ⇒ *MAVLink Console*.

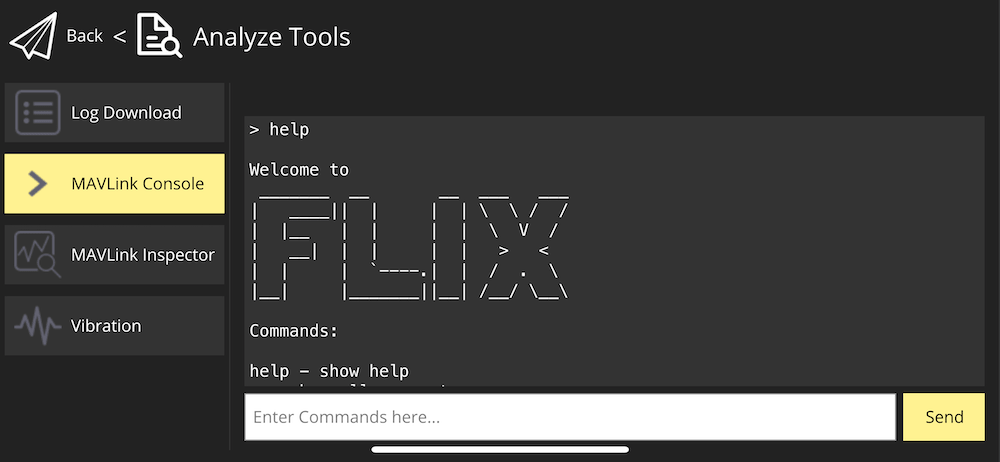
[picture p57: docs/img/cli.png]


> [!TIP]
> Use `help` command to see the list of available commands.

### Access parameters

The drone is configured using parameters. To access and modify them, go to the QGroundControl menu ⇒ *Vehicle Setup* ⇒ *Parameters*:

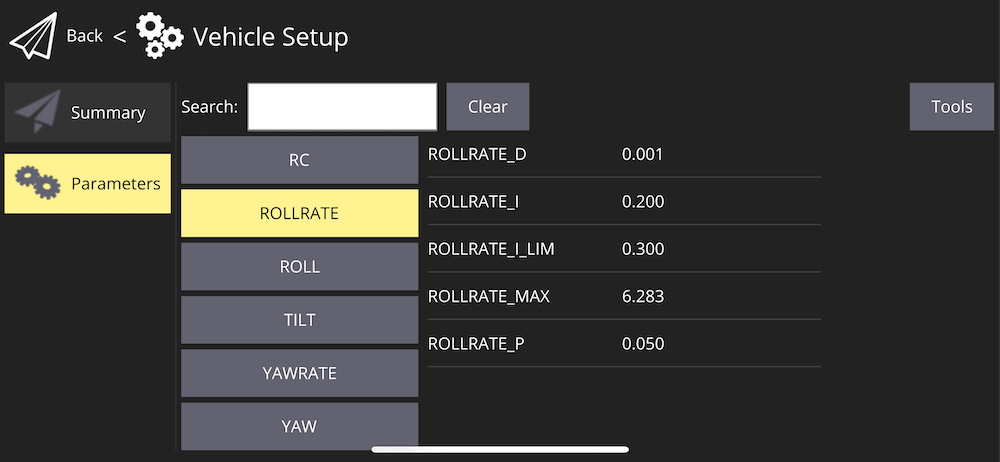
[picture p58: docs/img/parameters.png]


You can also work with parameters using `p` command in the console. Parameter names are case-insensitive.

### Configure the IMU

1. Configure the following parameters for the IMU:
   * `IMU_MODEL` — IMU model (1 for MPU-9250/MPU-6500, 2 for ICM-20948, 3 for MPU-6050, 4 for ICM-40609-D).
   * `IMU_BUS` — communication bus (0 for SPI, 1 for I²C).
   * `IMU_PIN_SCK`, `IMU_PIN_MISO`, `IMU_PIN_MOSI`, `IMU_PIN_CS` — SPI pin numbers.
   * `IMU_PIN_SCL`, `IMU_PIN_SDA` — I²C pin numbers.
   * `IMU_PIN_INT` — IMU data ready pin number (-1 if not used).
2. Reboot the drone.
3. Check the IMU is working using `imu` command in the console (should print `status: OK`).

### Define IMU orientation

The IMU orientation (relative to the drone's axes) is defined using the parameters: `IMU_ROT_ROLL`, `IMU_ROT_PITCH`, and `IMU_ROT_YAW`.

The drone has *X* axis pointing forward, *Y* axis pointing left, and *Z* axis pointing up, and the supported IMU boards have *X* axis pointing to the mounting holes side and *Z* axis pointing up from the component side:

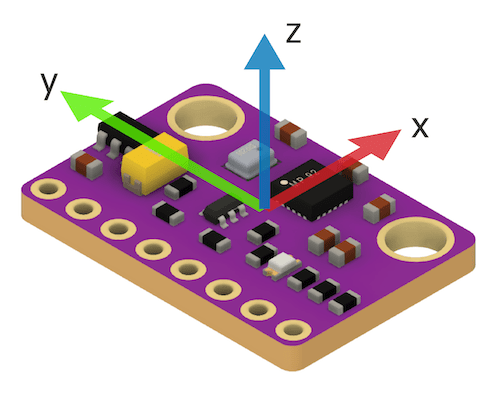
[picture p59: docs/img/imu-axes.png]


Use the following table to set the parameters for common IMU orientations:

|Orientation|Parameters|Orientation|Parameters|
|:-:|-|-|-|
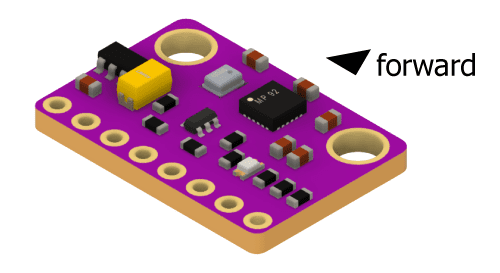
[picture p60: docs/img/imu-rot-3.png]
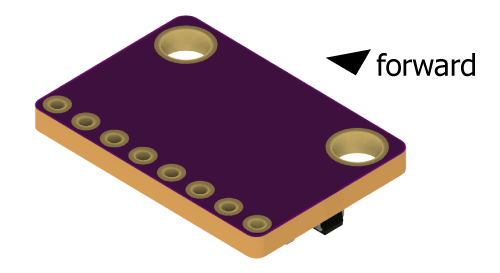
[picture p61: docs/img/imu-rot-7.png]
||`IMU_ROT_ROLL` = 0<br>`IMU_ROT_PITCH` = 0<br>`IMU_ROT_YAW` = 0 ||`IMU_ROT_ROLL` = 3.142<br>`IMU_ROT_PITCH` = 0<br>`IMU_ROT_YAW` = 0|
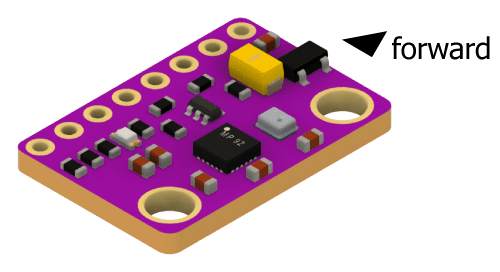
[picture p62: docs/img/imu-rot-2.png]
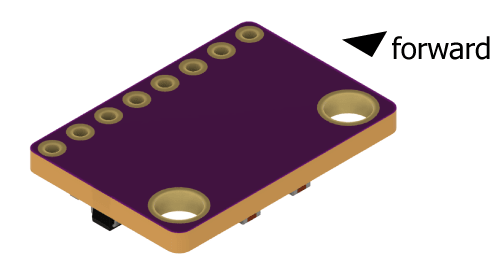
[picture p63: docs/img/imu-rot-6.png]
||`IMU_ROT_ROLL` = 0<br>`IMU_ROT_PITCH` = 0<br>`IMU_ROT_YAW` = -1.571||`IMU_ROT_ROLL` = 3.142<br>`IMU_ROT_PITCH` = 0<br>`IMU_ROT_YAW` = -1.571|
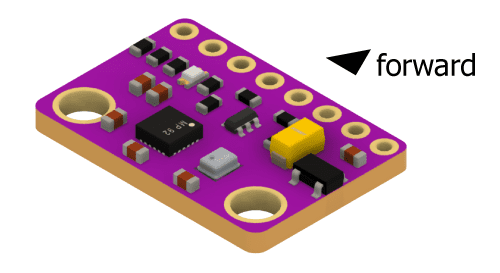
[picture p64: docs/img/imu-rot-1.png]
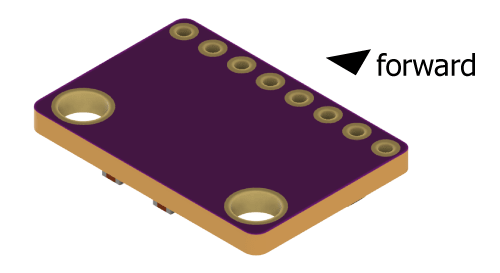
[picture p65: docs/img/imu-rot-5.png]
||`IMU_ROT_ROLL` = 0<br>`IMU_ROT_PITCH` = 0<br>`IMU_ROT_YAW` = 3.142||`IMU_ROT_ROLL` = 3.142<br>`IMU_ROT_PITCH` = 0<br>`IMU_ROT_YAW` = 3.142|
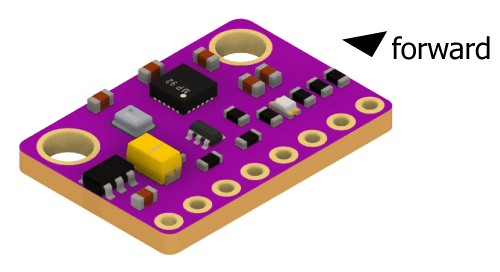
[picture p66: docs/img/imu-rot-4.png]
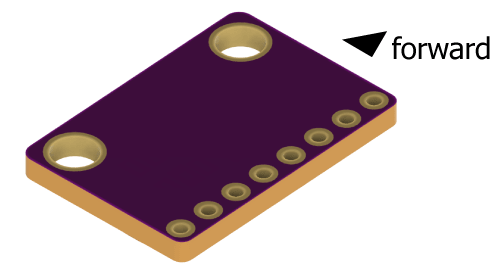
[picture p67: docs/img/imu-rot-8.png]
|<br>☑️ **Default**|<br>`IMU_ROT_ROLL` = 0<br>`IMU_ROT_PITCH` = 0<br>`IMU_ROT_YAW` = 1.571||`IMU_ROT_ROLL` = 3.142<br>`IMU_ROT_PITCH` = 0<br>`IMU_ROT_YAW` = 1.571|

### Calibrate accelerometer

Before flight you need to calibrate the accelerometer:

1. Access the console using QGroundControl (recommended) or Serial Monitor.
2. Type `ca` command there and follow the instructions.

### Setup motors

If using non-default motor pins, set the pin numbers using the parameters: `MOTOR_PIN_FL`, `MOTOR_PIN_FR`, `MOTOR_PIN_RL`, `MOTOR_PIN_RR` (front-left, front-right, rear-left, rear-right respectively).

#### Brushless motors

If using brushless motors with ESCs:

1. Set the appropriate PWM using the parameters: `MOT_PWM_STOP`, `MOT_PWM_MIN`, and `MOT_PWM_MAX` (1000, 1000, and 2000 is typical).
2. Decrease the PWM frequency using the `MOT_PWM_FREQ` parameter (400 is typical).

> [!CAUTION]
> **Remove the props when configuring the motors!** If improperly configured, you may not be able to stop them.

### Battery voltage monitoring (optional)

ESP32 ADC can measure only up to 3.3 V, so you need to use a voltage divider to monitor the battery voltage. To enable voltage measurement, set the following parameters:

1. `PWR_VOLT_PIN` — GPIO pin number where the voltage divider is connected (*-1* to disable).
2. `PWR_VOLT_SCALE` — voltage divider coefficient (*2* for two equal resistors).

After this setup, you should see the battery voltage in QGroundControl top panel or using `pw` command in the console.

### Important: check everything works

1. Check the IMU is working: perform `imu` command in the console and check the output:

   * The `status` field should be `OK`.
   * The `rate` field should be about 1000 (Hz).
   * The `accel` and `gyro` fields should change as you move the drone.
   * The `accel bias` and `accel scale` fields should contain calibration parameters (not zeros and ones).
   * The `gyro bias` field should contain estimated gyro bias (not zeros).
   * The `landed` field should be `1` when the drone is still on the ground and `0` when you lift it up.

2. Check the attitude estimation: connect to the drone using QGroundControl, rotate the drone in different orientations and check if the attitude estimation shown in QGroundControl is correct. Compare your attitude indicator (in the *large vertical* mode) to the video:

   

3. Perform motor tests. Use the following commands **— remove the propellers before running the tests!**

   * `mfr` — rotate front right motor (counter-clockwise).
   * `mfl` — rotate front left motor (clockwise).
   * `mrl` — rotate rear left motor (counter-clockwise).
   * `mrr` — rotate rear right motor (clockwise).

   Make sure rotation directions and propeller types match the following diagram:

   

> [!WARNING]
> Never run the motors when powering the drone from USB, always use the battery for that.

## Setup remote control

There are several ways to control the drone's flight: using **smartphone** (Wi-Fi), using **SBUS remote control**, or using **USB remote control** (Wi-Fi/ESP-NOW).

### Control with a smartphone

#### Using Mavlink Joystick app (Android)



1. Download and install [Mavlink Joystick app](https://github.com/goldarte/mavlink-joystick/releases/latest).
2. Power the drone using the battery.
3. Connect your smartphone to the appeared `flix` Wi-Fi network (password: `flixwifi`).
4. Open Mavlink Joystick app. It should connect and begin showing the drone's telemetry automatically.
5. Use the virtual joystick to fly the drone!

#### Using QGroundControl app

1. Install [QGroundControl mobile app](https://docs.qgroundcontrol.com/master/en/qgc-user-guide/getting_started/download_and_install.html#android) on your smartphone.
2. Power the drone using the battery.
3. Connect your smartphone to the appeared `flix` Wi-Fi network (password: `flixwifi`).
4. Open QGroundControl app. It should connect and begin showing the drone's telemetry automatically.
5. Go to the settings and enable *Virtual Joystick*. *Auto-Center Throttle* setting **should be disabled**.
6. Use the virtual joystick to fly the drone!

> [!TIP]
> Decrease `CTL_ATT_MAX` parameter when flying using the smartphone to make the controls less sensitive.

### Control with a remote control

If using SBUS-connected remote control you need to enable SBUS and calibrate it:

1. Connect to the drone using QGroundControl.
2. In parameters, set the `RC_RX_PIN` parameter to the GPIO pin number where the SBUS signal is connected, for example: 4. Negative value disables SBUS.
3. Check if the receiver is working using `rc` command in the console.
4. Open the console, type `cr` command and follow the instructions to calibrate the remote control.
5. Use the remote control to fly the drone!

### Control with a USB remote control

If your drone doesn't have RC receiver installed, you can use USB remote control and QGroundControl app to fly it.

1. Install [QGroundControl](https://docs.qgroundcontrol.com/master/en/qgc-user-guide/getting_started/download_and_install.html) app on your computer.
2. Connect your USB remote control to the computer.
3. Power up the drone.
4. Connect your computer to the appeared `flix` Wi-Fi network (password: `flixwifi`).
5. Launch QGroundControl app. It should connect and begin showing the drone's telemetry automatically.
6. Go to the QGroundControl menu ⇒ *Vehicle Setup* ⇒ *Joystick*. Calibrate your USB remote control there.
7. Use the USB remote control to fly the drone!

## Flight

For both virtual sticks and a physical joystick, the default control scheme is left stick for throttle and yaw and right stick for pitch and roll:



### Arming and disarming

To start the motors, you should **arm** the drone. To do that, move the left stick to the bottom right corner:



After that, the motors **will start spinning** at low speed, indicating that the drone is armed and ready to fly.

When finished flying, **disarm** the drone, moving the left stick to the bottom left corner:



> [!NOTE]
> If something goes wrong, go to the [Troubleshooting](troubleshooting.md) article.

### Flight modes

Flight mode is changed using mode switch on the remote control (if configured) or using the console commands. The main flight mode is *STAB*. In order to change modes using SBUS remote control, set the parameters: `CTL_FLT_MODE_0`, `CTL_FLT_MODE_1`, and `CTL_FLT_MODE_2` to required mode numbers (0 for *RAW*, 1 for *ACRO*, 2 for *STAB*, 3 for *AUTO*).

#### STAB

In this mode, the drone stabilizes its attitude (orientation). The left stick controls throttle and yaw rate, the right stick controls pitch and roll angles.

> [!IMPORTANT]
> The drone doesn't stabilize its position, so slight drift is possible. The pilot should compensate it manually.

#### ACRO

In this mode, the pilot controls the angular rates. This control method is difficult to fly and mostly used in FPV racing.

#### RAW

*RAW* mode disables all the stabilization, and the pilot inputs are mixed directly to the motors. The IMU sensor is not involved. This mode is intended for testing and demonstration purposes only, and basically the drone **cannot fly in this mode**.

#### AUTO

In this mode, the pilot inputs are ignored (except the mode switch). The drone can be controlled using [pyflix](../tools/pyflix/) Python library, or by modifying the firmware to implement the needed behavior.

If the pilot moves the control sticks and mode switch is not configured, the drone will switch back to *STAB* mode.

## Wi-Fi configuration

You can configure the Wi-Fi using parameters and console commands.

The Wi-Fi mode is chosen using `WIFI_MODE` parameter in QGroundControl or in the console:

* `0` — Wi-Fi is disabled.
* `1` — Access Point mode *(AP)* — the drone creates a Wi-Fi network.
* `2` — Client mode *(STA)* — the drone connects to an existing Wi-Fi network (may cause additional delays, so generally not recommended).
* `3` — ESP-NOW mode — the drone uses ESP-NOW protocol for communication.

The SSID and password are configured using the `ap` and `sta` console commands:

```
ap <ssid> <password>
sta <ssid> <password>
```

Example of configuring the Access Point mode:

```
ap my-flix-ssid mypassword123
p WIFI_MODE 1
```

Disabling Wi-Fi:

```
p WIFI_MODE 0
```

### Using ESP-NOW

[ESP-NOW](https://docs.espressif.com/projects/esp-idf/en/stable/esp32/api-reference/network/esp_now.html) is a low level wireless communication protocol. It can provide lower latency, better reliability, and longer range than Wi-Fi. However, it requires a second ESP32 board to be used as a proxy for the computer.

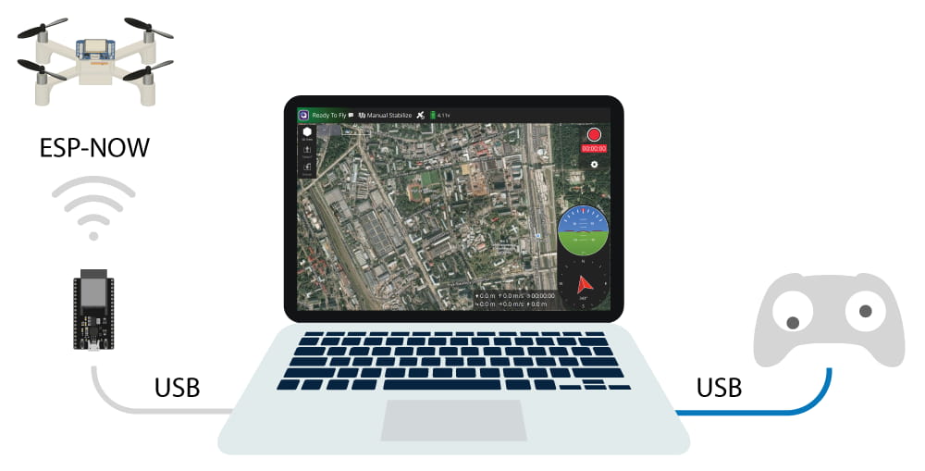
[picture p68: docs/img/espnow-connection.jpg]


To setup ESP-NOW communication:

1. Flash the second ESP32 board with ESP-NOW proxy sketch: [`tools/espnow-proxy/espnow-proxy.ino`](../tools/espnow-proxy/espnow-proxy.ino). Use Arduino IDE or command line: `make upload_proxy`.

2. Open Serial Monitor in Arduino IDE or use `make monitor` command. The ESP32 will print its MAC address and generated encryption key, for example:

   ```
   espnow 7a:c8:e3:eb:bf:e9 &PiuSysxP9+$L&5E
   ```

   Run this line as a console command on each drone you want to bind to this proxy board. [The maximum number](https://github.com/espressif/esp-idf/blob/e95cab4be8fd293e3f3323181e7a2280874da6f7/components/esp_wifi/include/esp_now.h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) of simultaneously connected drones is 20 (unencrypted) or 6 (encrypted).

3. Set the `WIFI_MODE` parameter to `3` on the drone:

   ```
   p WIFI_MODE 3
   ```

4. Go to the QGroundControl menu ⇒ *Application Settings* ⇒ *Comm Links*, add new link with the following settings:
   * Name: ESP32.
   * Type: Serial.
   * Serial Port: choose the port of the proxy ESP32 board, e. g. `/dev/cu.usbserial-0001`.
   * Baud Rate: 115200.
5. Click *Save*, click *Connect*. QGroundControl should connect to the drone using ESP-NOW and begin showing the telemetry.

> [!TIP]
> Make sure Arduino IDE is not running when using ESP-NOW proxy board, as it may block the serial port.

## Flight log

After the flight, you can download the flight log wirelessly for analysis. Use the following command on your computer for that:

```bash
make log
```

See more details about log analysis in the [log analysis](log.md) article.

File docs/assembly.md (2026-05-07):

# Brief assembly guide

Soldered components ([schematics variant](https://miro.com/app/board/uXjVN-dTjoo=/?moveToWidget=3458764612338222067&cot=14)):

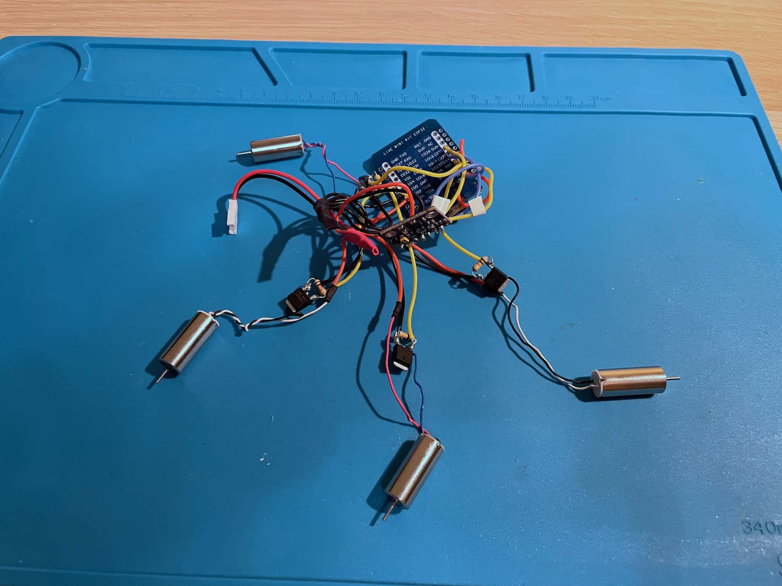
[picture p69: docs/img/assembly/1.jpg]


<br>Use double-sided tape to attach ESP32 to the top frame part (ESP32 holder):

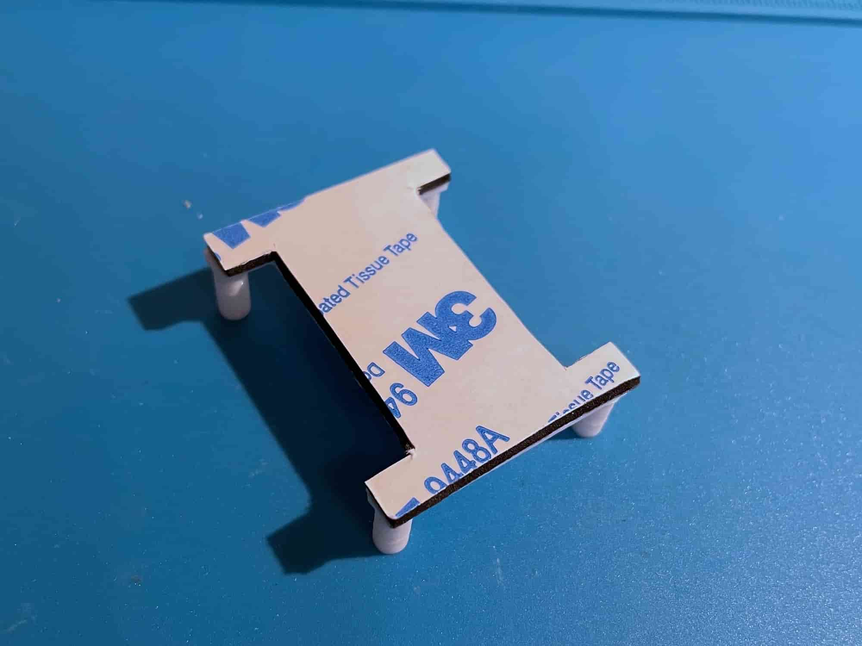
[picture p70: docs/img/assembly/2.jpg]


<br>Use two washers to screw the IMU board to the frame:

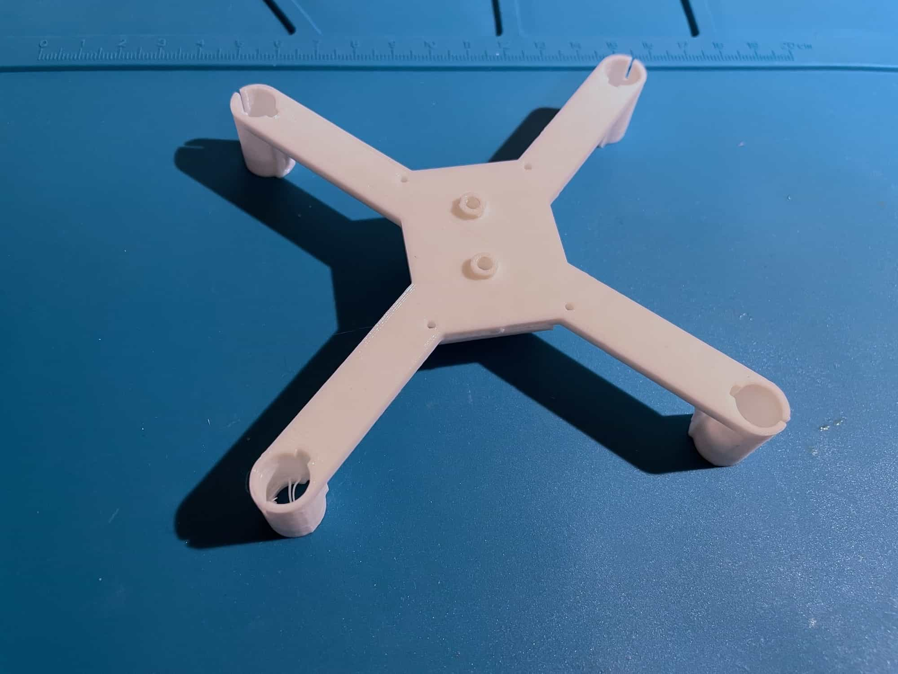
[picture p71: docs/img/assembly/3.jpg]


<br>Screw the IMU with M3x5 screws as shown:

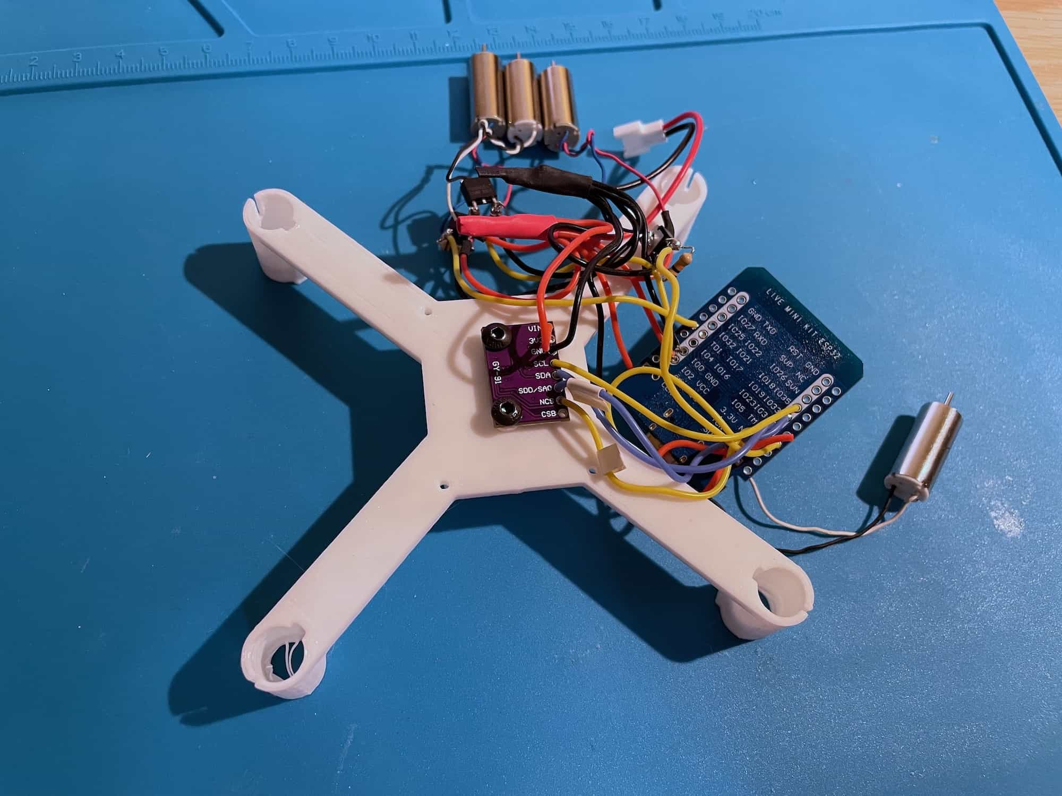
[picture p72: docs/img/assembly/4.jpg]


<br>Install the motors, attach MOSFETs to the frame using tape:

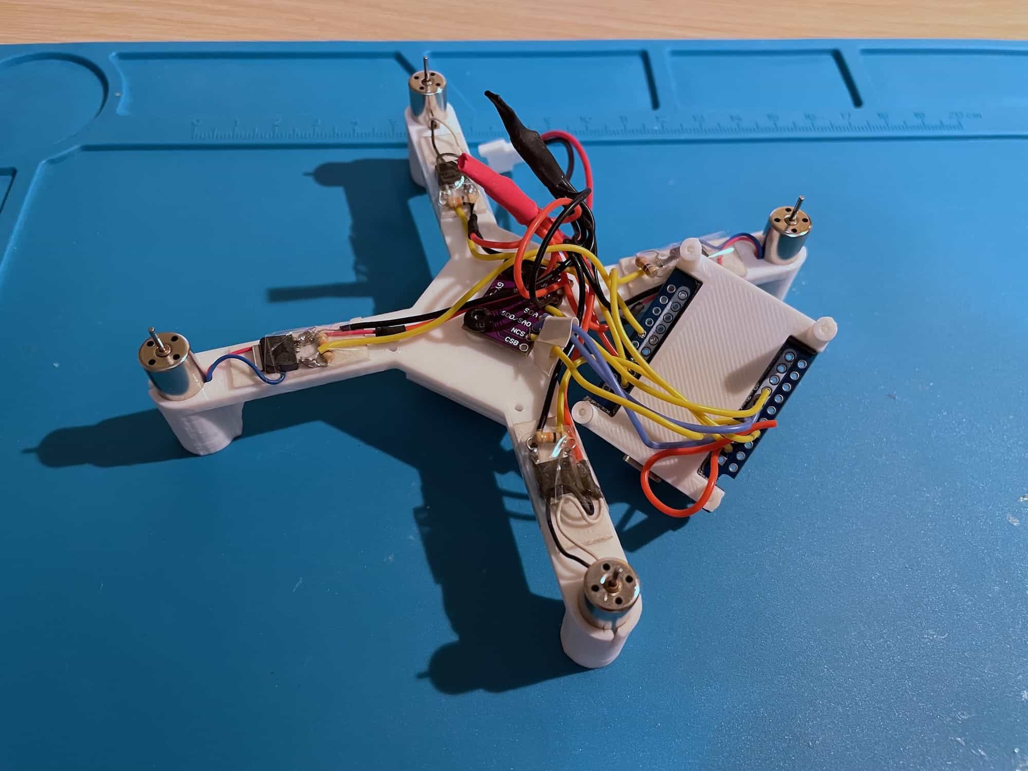
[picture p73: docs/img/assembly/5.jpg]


<br>Screw the ESP32 holder with M1.4x5 screws to the frame:

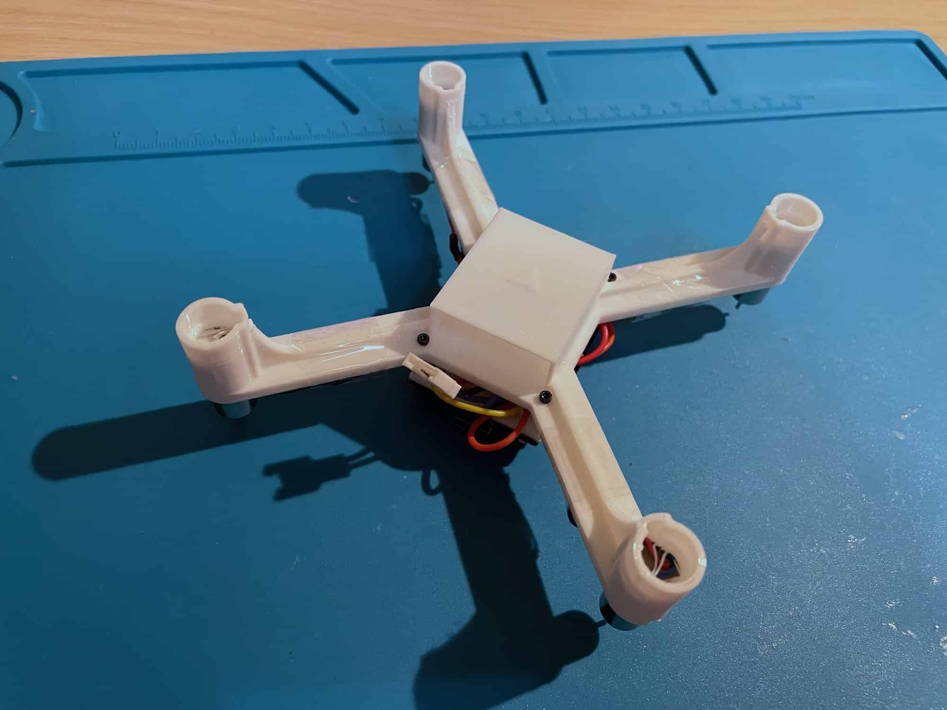
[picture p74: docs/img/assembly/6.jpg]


<br>Assembled drone:

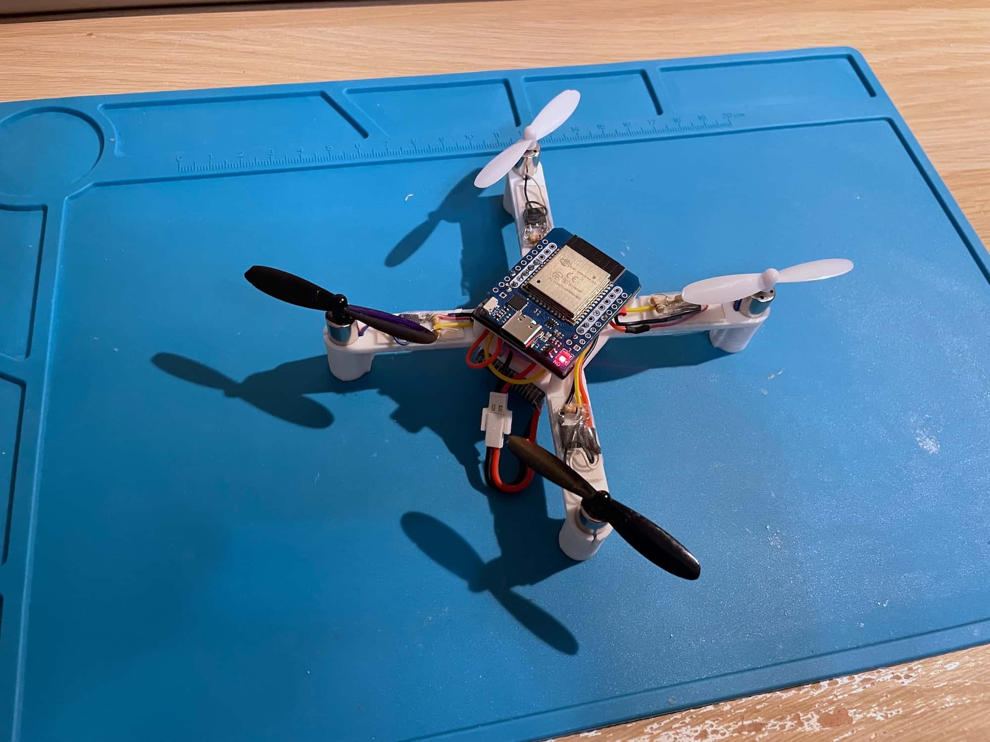
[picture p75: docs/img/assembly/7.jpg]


See an alternative assembly process photos here: https://drive.google.com/drive/folders/1FG5BH9RCzdf1XmJcC70PymiRMXcz6Fx7?usp=sharing.

## Motor directions

> [!WARNING]
> The drone above is an early build, and it has **inversed** motor directions scheme. The photos only illustrate the assembly process in general.

Use standard motor directions scheme:



Motors connection table:

|Motor|Position|Direction|Prop type|Motor wires|GPIO|
|-|-|-|-|-|-|
|Motor 0|Rear left|Counter-clockwise|B|Black & White|GPIO12 *(TDI)*|
|Motor 1|Rear right|Clockwise|A|Blue & Red|GPIO13 *(TCK)*|
|Motor 2|Front right|Counter-clockwise|B|Black & White|GPIO14 *(TMS)*|
|Motor 3|Front left|Clockwise|A|Blue & Red|GPIO15 *(TD0)*|

## Motors tightening

Motors should be installed very tightly — any vibration may lead to bad attitude estimation and unstable flight. If motors are loose, use tiny tape pieces to fix them tightly as shown below:

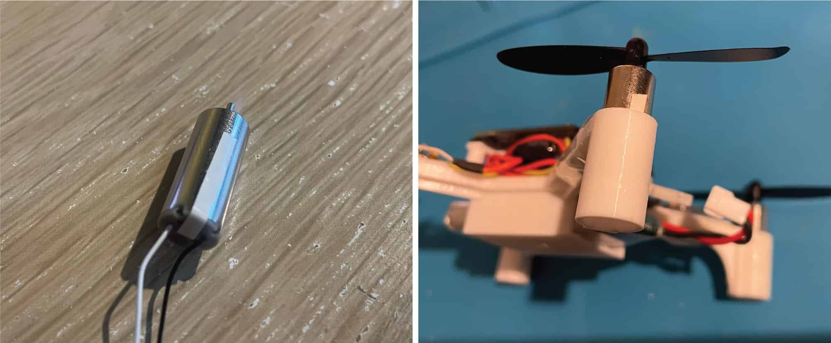
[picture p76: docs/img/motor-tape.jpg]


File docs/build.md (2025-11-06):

<!-- markdownlint-disable MD041 -->
Build instructions are moved to [usage article](usage.md).

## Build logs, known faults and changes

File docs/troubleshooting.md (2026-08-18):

# Troubleshooting

## The sketch doesn't compile

Do the following:

* **Check ESP32 core is installed**. Check if the version matches the one used in the [tutorial](usage.md#building-the-firmware).
* **Check libraries**. Install all the required libraries from the tutorial. Make sure there are no MPU-9250 or other peripherals libraries that may conflict with the ones used in the tutorial.
* **Check the chosen board**. The correct board to choose in Arduino IDE for ESP32 Mini is *WEMOS D1 MINI ESP32*.

## The drone doesn't fly

Do the following:

* **Check the battery voltage**. Use a multimeter to measure the battery voltage. The fully charged battery should have about 4.2V.
* **Check the battery you use has enough discharge current**. The battery should be able to provide 15A of current. So the C-rating for a 1000 mAh battery should be at least 15C (higher is better).
* **Check if there are some startup errors**. Connect the ESP32 to the computer and check the Serial Monitor output. Use the Reset button or `reboot` command to see the whole startup output.
* **Check the baudrate is correct**. If you see garbage characters in the Serial Monitor, make sure the baudrate is set to 115200.
* **Check if the console is working**. Perform `help` command in Serial Monitor. You should see the list of available commands. You can also access the console using QGroundControl *(Vehicle Setup* ⇒ *Analyze Tools* ⇒ *MAVLink Console)*.
* **Configure QGroundControl correctly before connecting to the drone** if you use it to control the drone. Go to the settings and enable *Virtual Joystick*. *Auto-Center Throttle* setting **should be disabled**.
* **If QGroundControl doesn't connect**, you might need to disable the firewall and/or VPN on your computer.
* **Make sure correct IMU model is chosen**. If using ICM-20948/MPU-6050 board, change `MPU9250` to `ICM20948`/`MPU6050` in the `imu.ino` file.
* **Check the IMU is working**. Perform `imu` command and check its output:
  * The `status` field should be `OK`.
  * The `rate` field should be about 1000 (Hz).
  * The `accel` and `gyro` fields should change as you move the drone.
* **Check the IMU orientation is set correctly**. If the attitude estimation is rotated, set the correct IMU orientation as described in the [tutorial](usage.md#define-imu-orientation).
* **Calibrate the accelerometer.** if is wasn't done before. Type `ca` command in Serial Monitor and follow the instructions.
* **Check the attitude estimation**. Connect to the drone using QGroundControl. Rotate the drone in different orientations and check if the attitude estimation is shown exactly as on the video below:

  

* **Check the IMU output**. Connect to the drone using QGroundControl on your computer. Go to the *Analyze* tab, *MAVLINK Inspector*. Plot the data from the `SCALED_IMU` message. The gyroscope and accelerometer data should change according to the drone movement.
* **Check the motors type**. Motors with exact 3.7V voltage are needed, not ranged working voltage (3.7V — 6V).
* **Check the motors**. Perform the following commands using Serial Monitor:
  * `mfr` — should rotate front right motor (counter-clockwise).
  * `mfl` — should rotate front left motor (clockwise).
  * `mrl` — should rotate rear left motor (counter-clockwise).
  * `mrr` — should rotate rear right motor (clockwise).
* **Check the propeller directions are correct**. Make sure your propeller types (A or B) are installed as on the picture:

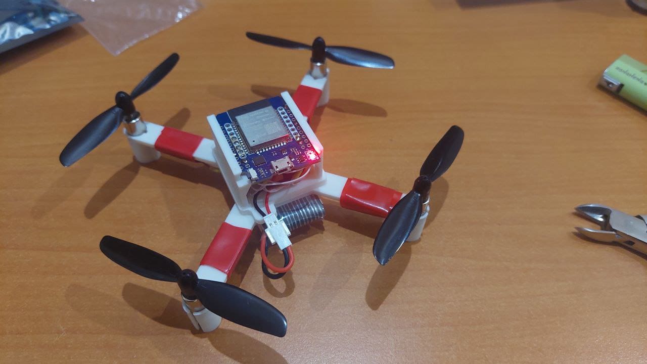
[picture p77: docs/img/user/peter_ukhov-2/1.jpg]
  

* **If using an SBUS receiver**:
  * **Define the used GPIO pin** in `RC_RX_PIN` parameter.
  * **Calibrate the RC** using `cr` command in the console.
  * **Check the controls** using `rc` command. All the controls should change between -1 and 1, and the throttle between 0 and 1.

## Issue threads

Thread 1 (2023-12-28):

Dependencies for the MAVLINK library

ukhov79, 2023-12-28:
It would be cool to add dependencies for the MAVLINK library:
https://github.com/mavlink/c_library_v2

okalachev, 2023-12-28:
You're absolutely correct, now this dependency handling totally missing. I was thinking about how I would handle it, using github submodules or download in `Makefile`, and now I'm planning to add downloading with the `Makefile` (I don't like submodules).

okalachev, 2023-12-28:
If you want to build with Wi-Fi and MAVLink, you may download MAVLink library manually and put it to the `flix` directory.

ukhov79, 2023-12-29:
Yes, I did. everything worked perfectly. Thanks!
However, my Arduino IDE sometimes refuses to upload code to the board and I have to restart IDE.
Have you thought about using platformio-ide and vs code? It seems easier to manage dependencies and libraries there.

okalachev, 2023-12-29:
I guess the recommended way to edit this code for experienced developers is using VSCode and console for building and uploading. I have VSCode config files that make IntelliSense work with the Arduino code and the simulation code, I just have not committed them yet (they are not portable enough).

okalachev, 2024-01-04:
@ukhov79, I decided to solve this in a radical way, without using submodules or Makefile downloads. I created an [Arduino library](https://github.com/okalachev/mavlink-arduino) that allows to install MAVLink in an easy Arduino way, and utilized it in this project.

So if you can check if it works, that would be helpful.

ukhov79, 2024-01-04:
Great solution! It works!

Closed 2024-01-04.

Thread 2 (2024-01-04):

Get rid of MPU9250 library fork

okalachev, 2024-01-04:
Don't use a fork here: https://github.com/okalachev/flix/blob/master/Makefile#L19.

It doesn't allow to install all libraries using Arduino IDE or `sketch.yaml`.

Depends on: https://github.com/bolderflight/invensense-imu/issues/123.

Closed 2024-01-05.

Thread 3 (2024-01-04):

Add circuit diagram

ukhov79, 2024-01-04:
I made an circuit diagram for assembly, but with a different receiver.
Maybe add it for those who want to build a quadcopter?
I will test it completely no earlier than mid-January. I'm waiting for parts from Aliexpress...
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

okalachev, 2024-01-04:
Hi, I would like to keep the visual style of all the diagrams consistent (as I'm thinking of making something like a textbook, article, or whatever).

But, since for now, there is absolutely no complete circuit diagram for the project, I added a link to your version to the readme as a user-contributed schematics.

okalachev, 2024-01-06:
There is an issue in this diagram: RC receiver should be connected to `u2RXD` (UART 2), not to `RXD` (UART 0).

ukhov79, 2024-01-06:
Thanks! I have adjusted the diagram.
I will make adjustments as I build. [Link to diagram in Miro](https://miro.com/app/board/uXjVN-dTjoo=/?share_link_id=904928044157).
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

ukhov79, 2024-01-30:
Final version with esp32 power issues.
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

Closed 2024-01-04.

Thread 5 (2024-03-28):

Small value with calibrateAccel

Igor743646, 2024-03-28:
0.3 second is to small for wating:
[    Serial.println("Cal accel: upside down"); delay(300);](https://github.com/okalachev/flix/blob/44ed3cf42c74d6015a9d6399044edf75b559b195/flix/imu.ino#L69)

okalachev, 2024-03-28:
Hi, it's an old version of the code. In the current version it [waits until enter is pressed](https://github.com/okalachev/flix/blob/fff7262d1bb5c3657cab2ba480ca9db5483a8ac4/flix/imu.ino#L70C40-L70C68).

ukhov79, 2024-03-29:
Could you update run-sim branch? I think it is there.

okalachev, 2024-03-29:
@ukhov79, hi you should not use run-sim branch, this branch is only for adding a feature of running the sim in CI (for testing). There is nothing useful for users in this branch.

Closed 2024-03-30.

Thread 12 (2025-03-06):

Not an issue

coppaxamsukk, 2025-03-06:
Can i use other board(ie. Esp32 dev board, esp32 s3,xiau esp32 s3, or esp32 c3) for this project? Will it fit in 3d printed frame?

Note: in my area esp32 d1 mini is not available

coppaxamsukk, 2025-03-06:
I saw a project in hall of fame using esp32 c3

okalachev, 2025-03-06:
ESP32-S3 is recommended as a replace, I'm doing a PCB based on this chip.

coppaxamsukk, 2025-03-13:
> ESP32-S3 is recommended as a replace, I'm doing a PCB based on this chip.

Which material i have to use for 3d printing? Someone said nylon but I'm afraid that's not available in my region (i don't own printer I'm gonna use 3rd party )

coppaxamsukk, 2025-03-13:
> ESP32-S3 is recommended as a replace, I'm doing a PCB based on this chip.

This code will work with esp32 s3(xiau edition? That's small) without any modifications? And
Which material i have to use for 3d printing? Someone said nylon but I'm afraid that's not available in my region (i don't own printer I'm gonna use 3rd party )

okalachev, 2025-03-13:
You can use any standard material, like PLA or PETG.
ESP32-C3 is somewhat supported, if you have problems with running or compiling, create an issue or ask in [Telegram chat](https://t.me/opensourcequadcopterchat).

coppaxamsukk, 2025-03-14:
> You can use any standard material, like PLA or PETG. ESP32-C3 is somewhat supported, if you have problems with running or compiling, create an issue or ask in [Telegram chat](https://t.me/opensourcequadcopterchat).

Okay, i will ask in telegram,  someone in hall of fame used c3 that looked awesome so i wanna make it.

Thanks for reply closing issue.

Closed 2025-03-14.

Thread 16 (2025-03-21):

Using other MPU’s

furrywall, 2025-03-21:
Is it possible to use other mpu’s like the mpu6050

okalachev, 2025-03-22:
No, there is no support for MPU-6050. For now, the supported IMUs are MPU‑9250, MPU‑6500 and ICM‑20948. Later I will add support for ICM-42688-P.

You can take any Arduino library for MPU-6050 and change `imu.ino` so it uses this library, or add support for this IMU to my [FlixPeriph](https://github.com/okalachev/flixperiph) library.

Closed 2025-03-23.

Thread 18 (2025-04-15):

replacement for DF500 reiever

hermanumrao, 2025-04-15:
hey, so do you think i can use FSi6s receiver instead of DF500
i was thinking to open up the case to reduce wait and then use it

do you think it will work, also what code changes do you think might be required???

okalachev, 2025-04-15:
Hi! Any receiver that supports SBUS protocol can be used.

Closed 2025-04-18.

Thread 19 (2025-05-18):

QGroundControl crashes immediately after connect.

mameniac, 2025-05-18:
Starting the app works perfectly fine as long as no "server" or drone is connected.
However, as soon as I start the simulation server, QGroundControl crashes—regardless of whether it's running on Windows or Android.

At first, I thought the issue was related to my VM running Ubuntu 22.04 (as described in the instructions).
So I uploaded the code to my ESP32 and powered it on. The Wi-Fi network appears, and I’m able to connect to it without any problems.

But when I launch QGroundControl on my Android device while the drone is powered on, the app crashes immediately.
If I disconnect the drone from power and then open QGroundControl, it runs just fine. Yet, the moment I power the drone back on, QGroundControl crashes again.

I really don’t understand what’s going wrong here.
Interestingly, when I use a Windows PC and connect to the simulation running on my VM, it works—but the performance is extremely poor.

That’s why I decided to test everything directly using the drone instead of relying on the emulation.

Any suggestions ?

okalachev, 2025-05-18:
Hi, which version of QGroundControl do you use?

mameniac, 2025-05-18:
I tried the latest stable, and the latest nighlty build. Both do the same.
Same with the Arduino app (also latest version). Got them both fresh from the QGC site.
It always crah with an error c0000005 = Access Violation.

okalachev, 2025-05-18:
I used the latest release candidate version of QGC (5.0) in macOS, and it indeed crashes after connection. Don't know what causes this bug QGC RC 5.0

But with the stable version 4.4.3 it works without any problems.

Anyway, the Flix firmware doesn't send anything problematic, only very basic mavlink messages. You can see them here:

https://github.com/okalachev/flix/blob/be7b6ec0c9b7fcf41c633c9319c9c8275ad089d9/flix/mavlink.ino#L26

You can try to disable sending some of the messages to investigate, what message causes QGC to crash. But it seems like a bug in QGC. There is nothing incorrect in Flix mavlink stream (and even if it was, QGC should not crash out of it). I you found the message causing the crash, it would be good to create an issue in [QGC repo](https://github.com/mavlink/qgroundcontrol).

mameniac, 2025-05-18:
That solved the problem so far mor me. Version 4.4.3 works like a charm. The mobile app as well. So I managed to get that thing in the air, my batterie died and it crashed, BUT : it's moving !
Is there a way to connect a XBox-Joystick to fly that thing manually ?
I really appreciate your help !

okalachev, 2025-05-19:
Good, I guess an issue should be created in QGC, if there is a bug in the RC version.

You can connect any USB joystick supported by the OS to a desktop computer, run QGC, connect to the drone, and the QGC will detect it and use it as a drone controller. This is described here: https://github.com/okalachev/flix/blob/master/docs/build.md#control-with-usb-remote-control-1.

Also, send your build description to the user builds article: https://github.com/okalachev/flix/blob/master/docs/user.md.

mameniac, 2025-05-19:
Again thank you.
I manages to connect the XBox Wireless Controller to QGC and the drone reacts, but right after spinning two motors it shuts down.
Even the calibration of the accelerometer is weird. It says its calibrated well (after running "ca") but in QGC the drone is always upside down. So probably something went wrong with my gyro.

mameniac, 2025-05-20:
As I fixed the gyro, its not upside down anymore.
I re-wired the drone as intended and made an extra plus and minus terminal with a small pcb. So I can sure that everything is connected to the battery directly.
Battery is an 3,7V 200mAh LiPo and the wiring is 100% made like in the schematics said.
Problem is : Motor test works, but right after each test, the drone boots up again.
Using QGC : all 4 Motor spin up and the the drone disconnects and is dead. Needs to be power-cycled.
That makes absolute no sense to me.
All parts used are from your BOM and the wiring is 1:1 lkike in the schematics.
Battery connector : Plus -> power the ESP . From ESP down to gyro and directly to plus terminal of each motor
Minus/GND : to ESP and from there to gyro and to the mosfets.
Gyro connections to ESP are fine, because its working.
I powered with an power-supply as well to be sure there are enough amps. (Cable diameter is enough !)
Same behaviour.
I have no clue what is wrong. I changed ESP and gyro as well.
I would appreciate any help

Closed 2025-05-23.

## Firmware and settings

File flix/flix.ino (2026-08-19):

// Copyright (c) 2023 Oleg Kalachev <okalachev@gmail.com>
// Repository: https://github.com/okalachev/flix

// Main firmware file

#include "vector.h"
#include "quaternion.h"
#include "util.h"

extern float t, dt;
extern float controlRoll, controlPitch, controlYaw, controlThrottle, controlMode;
extern Vector gyro, acc;
extern Vector rates;
extern Quaternion attitude;
extern bool landed;
extern float motors[4];

void setup() {
	setupConsole();
	print("Initializing Flix\n");
	setupParameters();
	setupPower();
	setupLED();
	setLED(true);
	setupMotors();
	setupWiFi();
	setupIMU();
	setupRC();
	setLED(false);
	print("Initializing complete\n");
}

void loop() {
	readIMU();
	step();
	readRC();
	estimate();
	control();
	sendMotors();
	handleConsole();
	processMavlink();
	readVoltage();
	logData();
	syncParameters();
}

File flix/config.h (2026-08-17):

// Copyright (c) 2026 Oleg Kalachev <okalachev@gmail.com>
// Repository: https://github.com/okalachev/flix

// Parameter defaults

#pragma once

void setDefaults() {
	// Set defaults here

	#if defined(CONFIG_IDF_TARGET_ESP32S3) || defined(CONFIG_IDF_TARGET_ESP32C3)
		pwmFrequency = 38000;
	#endif

	#ifdef CONFIG_IDF_TARGET_ESP32
		// classic esp32 configuration
		motorPins[MOT_RL] = 12;
		motorPins[MOT_RR] = 13;
		motorPins[MOT_FR] = 14;
		motorPins[MOT_FL] = 15;
	#endif

	#ifdef FLIX2
		imuModel = 4; // ICM-40609-D
		imuIntPin = 10;
		imuCsPin = 14;
		voltagePin = 3;
		motorPins[MOT_RL] = 41;
		motorPins[MOT_RR] = 7;
		motorPins[MOT_FR] = 18;
		motorPins[MOT_FL] = 38;
	#endif
}

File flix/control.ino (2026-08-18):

// Copyright (c) 2023 Oleg Kalachev <okalachev@gmail.com>
// Repository: https://github.com/okalachev/flix

// Flight control

#include "vector.h"
#include "quaternion.h"
#include "pid.h"
#include "filter.h"
#include "util.h"

const int RAW = 0, ACRO = 1, STAB = 2, AUTO = 3; // flight modes
int mode = STAB;
bool armed = false;

Quaternion attitudeTarget;
Vector ratesTarget;
Vector ratesExtra; // feedforward rates
Vector torqueTarget;
float thrustTarget;

PID rollRatePID(0.05, 0.2, 0.001, 0.3, 0.2);
PID pitchRatePID(0.05, 0.2, 0.001, 0.3, 0.2);
PID yawRatePID(0.3, 0, 0, 0.3);
PID rollPID(6);
PID pitchPID(6);
PID yawPID(3);
Vector maxRate(radians(360), radians(360), radians(360));
float tiltMax = radians(30);
int flightModes[] = {STAB, STAB, STAB}; // map for rc mode switch

extern const int MOT_RL, MOT_RR, MOT_FR, MOT_FL;
extern float controlRoll, controlPitch, controlThrottle, controlYaw, controlMode;

void control() {
	interpretControls();
	failsafe();
	controlAttitude();
	controlRates();
	controlTorque();
}

void interpretControls() {
	if (controlMode < 0.25) mode = flightModes[0];
	else if (controlMode <= 0.75) mode = flightModes[1];
	else if (controlMode > 0.75) mode = flightModes[2];

	if (mode == AUTO) return; // pilot is not effective in AUTO mode

	if (controlThrottle < 0.05 && controlYaw > 0.95) armed = true; // arm gesture
	if (controlThrottle < 0.05 && controlYaw < -0.95) armed = false; // disarm gesture

	if (abs(controlYaw) < 0.1) controlYaw = 0; // yaw dead zone

	thrustTarget = controlThrottle;

	if (mode == STAB) {
		float yawTarget = attitudeTarget.getYaw();
		if (!armed || invalid(yawTarget) || controlYaw != 0) yawTarget = attitude.getYaw(); // reset yaw target
		attitudeTarget = Quaternion::fromEuler(Vector(controlRoll * tiltMax, controlPitch * tiltMax, yawTarget));
		ratesExtra = Vector(0, 0, -controlYaw * maxRate.z); // positive yaw stick means clockwise rotation in FLU
	}

	if (mode == ACRO) {
		attitudeTarget.invalidate(); // skip attitude control
		ratesTarget.x = controlRoll * maxRate.x;
		ratesTarget.y = controlPitch * maxRate.y;
		ratesTarget.z = -controlYaw * maxRate.z; // positive yaw stick means clockwise rotation in FLU
	}

	if (mode == RAW) { // direct torque control
		attitudeTarget.invalidate(); // skip attitude control
		ratesTarget.invalidate(); // skip rate control
		torqueTarget = Vector(controlRoll, controlPitch, -controlYaw) * 0.1;
	}
}

void controlAttitude() {
	if (!armed || attitudeTarget.invalid() || thrustTarget < 0.1) return; // skip attitude control

	const Vector up(0, 0, 1);
	Vector upActual = Quaternion::rotateVector(up, attitude);
	Vector upTarget = Quaternion::rotateVector(up, attitudeTarget);

	Vector error = Vector::rotationVectorBetween(upTarget, upActual);

	ratesTarget.x = rollPID.update(error.x) + ratesExtra.x;
	ratesTarget.y = pitchPID.update(error.y) + ratesExtra.y;

	float yawError = wrapAngle(attitudeTarget.getYaw() - attitude.getYaw());
	ratesTarget.z = yawPID.update(yawError) + ratesExtra.z;
}


void controlRates() {
	if (!armed || ratesTarget.invalid() || thrustTarget < 0.1) return; // skip rates control

	Vector error = ratesTarget - rates;

	// Calculate desired torque, where 0 - no torque, 1 - maximum possible torque
	torqueTarget.x = rollRatePID.update(error.x);
	torqueTarget.y = pitchRatePID.update(error.y);
	torqueTarget.z = yawRatePID.update(error.z);
}

void controlTorque() {
	if (!torqueTarget.valid()) return; // skip torque control

	if (!armed) {
		for (float& m : motors) m = 0; // stop motors if disarmed
		return;
	}

	if (thrustTarget < 0.1) {
		for (float& m : motors) m = 0.1; // idle thrust
		return;
	}

	motors[MOT_FL] = thrustTarget + torqueTarget.x - torqueTarget.y + torqueTarget.z;
	motors[MOT_FR] = thrustTarget - torqueTarget.x - torqueTarget.y - torqueTarget.z;
	motors[MOT_RL] = thrustTarget + torqueTarget.x + torqueTarget.y - torqueTarget.z;
	motors[MOT_RR] = thrustTarget - torqueTarget.x + torqueTarget.y + torqueTarget.z;

	desaturate(); // prioritize angle control over thrust control
}

void desaturate() {
	float max_ = -INFINITY, min_ = INFINITY;
	float correction = 0;

	// Find maximum and minimum thrust
	for (float m : motors) {
		if (m > max_) max_ = m;
		if (m < min_) min_ = m;
	}

	if (max_ > 1) { // thrust is above maximum
		correction = max_ - 1;
	} else if (min_ < 0) { // thrust is below minimum
		correction = min_;
	}

	for (float& m : motors) {
		m -= correction;
	}
}

const char* getModeName() {
	switch (mode) {
		case RAW: return "RAW";
		case ACRO: return "ACRO";
		case STAB: return "STAB";
		case AUTO: return "AUTO";
		default: return "UNKNOWN";
	}
}

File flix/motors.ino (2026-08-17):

// Copyright (c) 2023 Oleg Kalachev <okalachev@gmail.com>
// Repository: https://github.com/okalachev/flix

// PWM control for motors

#include "util.h"

float motors[4]; // normalized motor thrusts in range [0..1]

int motorPins[4] = {-1, -1, -1, -1}; // default pin numbers
int pwmFrequency = 78000;
int pwmResolution = 10;
int pwmStop = 0;
int pwmMin = 0;
int pwmMax = -1; // -1 means duty cycle mode

const int MOT_RL = 0, MOT_RR = 1, MOT_FR = 2, MOT_FL = 3;

void setupMotors() {
	print("Setup motors\n");
	// Configure pins
	for (int i = 0; i < 4; i++) {
		if (motorPins[i] < 0) continue; // skip unassigned motors
		ledcAttach(motorPins[i], pwmFrequency, pwmResolution);
		pwmFrequency = ledcChangeFrequency(motorPins[i], pwmFrequency, pwmResolution); // when reconfiguring
	}
	sendMotors();
}

void sendMotors() {
	for (int i = 0; i < 4; i++) {
		if (motorPins[i] < 0) continue; // skip unassigned motors
		ledcWrite(motorPins[i], getDutyCycle(motors[i]));
	}
}

int getDutyCycle(float value) {
	value = constrain(value, 0, 1);

	if (pwmMax >= 0) { // pwm mode
		float pwm = mapf(value, 0, 1, pwmMin, pwmMax);
		if (value == 0) pwm = pwmStop;
		float duty = mapf(pwm, 0, 1000000 / pwmFrequency, 0, (1 << pwmResolution) - 1);
		return round(duty);
	} else { // duty cycle mode
		return round(value * ((1 << pwmResolution) - 1));
	}
}

bool motorsActive() {
	return motors[0] != 0 || motors[1] != 0 || motors[2] != 0 || motors[3] != 0;
}

void testMotor(int n, float thrust) {
	print("Testing motor %d\n", n);
	motors[n] = thrust;
	delay(50); // ESP32 may need to wait until the end of the current cycle to change duty https://github.com/espressif/arduino-esp32/issues/5306
	sendMotors();
	pause(3);
	motors[n] = 0;
	sendMotors();
	print("Done\n");
}

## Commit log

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2023-03-26 Fix logging pointer overflow check
    [log.ino]
2023-04-08 Use own table model
    [linnmon.sdf]
2023-04-10 Fix the broken build related to arduino/arduino-cli#758
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2023-11-11 Some cleanups
    [floor.sdf]
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2023-11-11 Fix log period computation
    [log.ino]
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2023-11-12 Minor code cleanups and fixes
    [cli.ino, control.ino, log.ino]
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2023-12-03 dt can be negative on simulator reset
    [time.ino]
2023-12-03 Use simulated IMU noise values from MPU9250 datasheet
    [flix.sdf]
2023-12-10 Fix timestamp in mavlink, add imu message, cleanup
    [mavlink.ino]
2023-12-13 Add reset command to cli
    [cli.ino]
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2023-12-15 Correctly fill armed field in heartbeat mavlink message
    [mavlink.ino]
2023-12-15 Main sdf cleanups, minor fix
    [flix.sdf]
2023-12-19 Apply accelerometer in estimation only when we're landed and stable Accelerometer gives only motors specific force in flight, which makes it useless to determine the current vertial
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2024-01-04 Loose port detection wildcard to catch both CP2102 and CP2104 USB-UART bridges
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2024-01-05 #2 Use official MPU9250 library 1.0.2 The release was fixed https://github.com/bolderflight/invensense-imu/issues/123
2024-01-13 Fix actuator_output mavlink message generation
    [mavlink.ino]
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2024-01-17 Disable ESP32 reset on low voltage
    [flix.ino, util.ino]
2024-01-19 Don't calibrate gyro on start since MPU9250 library does that on begin
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2024-01-31 Fix RC_CHANNELS_SCALED inactive channel values They should be INT16_MAX not UINT16_MAX
    [mavlink.ino]
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2024-02-06 Fix vector, quaternion, pid and lpf libraries curly braces code style
2024-02-06 Correctly set output parameters of simulated SBUS::read, minor name fix
    [rc.ino]
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2024-02-20 Use more correct implementation of toEulerZYX fixing some yaw issues We actually need to use Tait–Bryan Z-Y-X angles, not classic Euler's
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2024-02-24 Use default recommended chip-select pin (GPIO5) for SPI Update link to the schematics #3 to the most recent version
2024-03-02 Fix reverse motors pwm
    [motors.ino]
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2024-03-11 Fix accel calibration upside down wait time
    [imu.ino]
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2024-03-15 Correctly restore IMU settings after accel calibration
    [imu.ino]
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2024-04-20 Transfer gyro low pass filter to estimate.ino Separate raw gyro data and filtered rates to different variables
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2024-05-21 Install arduino-cli to /usr/local/bin The Arduino docs probably has mistake offering non-existent ~/local/bin path instead of ~/.local/bin. Some systems lack ~/.local/bin as well, so simply use /usr/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
2024-05-21 Minor fixes and changes
    [control.ino]
2024-05-21 Fix PWM values for reverse rotations
    [motors.ino]
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2024-10-23 More clean yaw error calculation
    [control.ino]
2024-10-23 Remove ESC support and add MOSFET support in motors code The new version uses MOSFETs
2024-10-23 Use FLU as the main coordinate system instead of FRD Corresponding to the IMU orientation in the new version
2024-10-23 Keep the t variable monotonic in the simulation Otherwise it causes stopping sending MAVLink and other bugs
    [simulator.cpp]
2024-10-23 Update visual of the Gazebo model to the new version Use STL instead of DAE, make props separated visuals
    [flix.sdf, flix.stl]
2024-10-23 Move the visual part of the gazebo model to the bottom of the file
    [flix.sdf]
2024-10-23 Major documentation update, the new drone version files released
    [esp32-holder.stl, flix-frame.stl, washer-m3.stl]
2024-10-23 Fix Gazebo stl model orientation
    [flix.stl]
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2024-10-29 Upload STEP files for models
    [esp32-holder.step, flix-frame.step, washer-m3.step]
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2024-11-03 Remove LED horizontality signalization It's better to control the attitude estimation using QGC
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2024-11-04 Updates to LED control code Don't call digitaWrite on each setLED call
2024-11-04 Fix c_cpp_properties.json to match updated ESP32 core version
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2024-11-23 Fix non-working motor control commands
    [cli.ino]
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2024-11-27 Use the new UART2 pins for RC by default To make it consistent with the documentation
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2024-12-16 Create book and deploy it to the website (#6)
    * Create book structure.
    * Add workflow for linting the markdown using markdownlint.
    * Add workflow for building the book with mdBook and deploying to the website.
    * Restyle mdBook and support GitHub-style alerts.
    * Add images zooming.
    * Add index, firmware structure and gyroscope articles.
2024-12-20 Add CLI command for rebooting the drone
    [cli.ino]
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2024-12-22 Don't let throttle be less than 0 in failsafe
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2024-12-28 Some minor cleanups and fixes
    [imu.ino, parameters.ino, util.ino]
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2025-01-09 Implement `rotate` method for quaternions as replace for multiplication Vector rotating method is renamed from `rotate` to `rotateVector` to avoid inconsistent object and argument order in different 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
    [control.ino, estimate.ino]
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2025-01-09 Fix getDutyCycle return type to make it possible to increase resolution
    [motors.ino]
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2025-01-09 Make motor indexes definition const int and move them to motors.ino Remove motor indexes definitions from flix.ino Add motors.ino to simulation code and implement required mocks
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2025-01-10 Make max tilt and max angle rates MAVLink parameters Also decrease default max yaw rate to 300 degrees
2025-01-10 Global variables cleanups Remove unused PID objects for cli Move loopRate to time.ino
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2025-01-12 Increase motors PWM frequency to 1000 To match the main loop frequency
2025-01-12 Add missing const qualifiers
    [cli.ino]
2025-01-14 Check if requested parameters indexes are correct In case if gcs gets crazy and requests incorrect parameter index
    [parameters.ino]
2025-01-17 Minor cleanups and fixes
    [flix.ino, wifi.ino]
2025-01-17 Catch port bind error in simulation
    [wifi.h]
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2025-01-21 Add new frame models Version 1.1
    [flix-frame-1.1.step, flix-frame-1.1.stl]
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2025-01-24 Fix firmware build with Wi-Fi disabled
    [parameters.ino]
2025-01-24 Fix working on ESP32-S3 (#8)
    Disable brown-out detector in a more correct way: clear only enable bit instead of clearing the whole register.
    ---------
2025-01-24 Add failsafe to prevent arming without prior zero throttle
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2025-02-17 Refactor CLI submodule Move command parsing to doCommand Parse command with splitString instead of stringToken Trim commands Move cliTestMotor to the bottom Rename parseInput to handleInput, which is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
2025-02-18 Support MAVLink console Implement receiving and sending SERIAL_CONTROL message Use global defined print function instead of Serial.printf
2025-02-18 Fix accel calibration via mavlink console Add 5 s timeout as waiting for enter is not implemented for mavlink console yet
    [imu.ino]
2025-02-25 Check target system id in mavlink messages Skip messages addressed to other systems
    [mavlink.ino]
2025-02-27 Remove dt multiplier from acc correction and increase acc weight More classical complementary filter implementation Increase effective accelerometer weight for faster convergence
    [estimate.ino]
2025-02-28 Use natural order of ino files includes in simulation In Arduino, ino files are included in alphabetical order. Cleanup unused function declarations in simulation, add missing. Rename flu to frd func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
    [mavlink.ino, simulator.cpp]
2025-02-28 Fix mavlink disconnection in pauses in cli commands Implement pause function that proceeds processing mavlink. Use temporal workaround for simulation, as micros function gives the same result on the 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
    [cli.ino, imu.ino, motors.ino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]
2025-03-14 Encode if the mode in stabilized in heartbeat message
    [mavlink.ino]
2025-03-14 Minor code style fix
    [mavlink.ino]
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2025-03-29 Continuous gyro bias estimation (#17)
    Estimate gyro bias continuously instead of calibrating the gyro at startup.
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2025-04-12 Minor code simplifications
    [flix.sdf]
2025-04-24 Fix simulation build in Actions Switched runner to Ubuntu 22.04 since Gazebo 11 now has binaries for 22.04 (amd64 only). Changed the building tutorial to reflect that.
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2025-05-04 Make accelerometer calibration more verbose Print the number of each calibration step
2025-05-04 Make mavlink print buffered Combine all output of each step into one SERIAL_CONTROL message
2025-05-05 Add sys command Show ESP32 model and free heap Show tasks table with stack and cpu usage
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2025-05-06 Some cli improvements Improve loop rate formatting Show cpu temperature in sys command
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2025-05-10 Make cli command case insensitive iOS QGC capitalizes the command by default, so it's more convinient
2025-05-10 Revert sending mavlink udp packets in unicast This requires more complex approach as client ip may change between reconnections
    [wifi.ino]
2025-05-31 Improve vector and quaternion libraries Make the order or basic methods consistent between Vector and Quaternion. Remove `ZYX` from Euler method names as this is standard for robotics. Rename angular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
    [cli.ino, control.ino, estimate.ino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]
2025-06-19 Add missing newlines to initialization prints
    [flix.ino]
2025-06-30 Add missing includes to Arduino.h to make build more portable
2025-07-03 Increase motors pwm frequency to 78Khz 1000 Hz is too low frequency considering the update loop for motors signal is also 1000 Hz. Decrease resolution as it's required to set larger pwm frequencies. 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
    [motors.ino]
2025-07-12 Improve pause function work Fix disconnecting from qgc while pausing in the simulation. Consider total delay time in micros() in simulation to increase t while delaying. Simplify and get rid of ARDUI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
    [cli.ino]
2025-07-14 Major rework of rc subsystem Implement channels mapping calibration. Store mapping in parameters. Get rid of `controls` array and store control inputs in `controlRoll`, `controlPitch`, ... variables.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
    [cli.ino, control.ino, flix.ino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]
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2025-07-19 Fix rates, acc and gyro coordinate frame in mavlink All of them should be in frd. Get rid of fluToFrd function - there is no big need for it.
    [mavlink.ino]
2025-07-21 Increase connection timeout for arduino-cli as it prevents some users from downloading the core
2025-07-28 Add missing set_velocity method stub to pyflix
    [flix.py]
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2025-08-25 Refactor control subsystem Add interpretControls function to convert pilot commands and mode into control targets and make control functions independent from the mode. Add ratesExtra target for rates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
2025-08-26 Add cli commands for switching mode Make mode variable int instead of enum, which is more convinient.
2025-08-27 Refactor arming logic Arm and disarm with gestures only: left stick right/down for arming, left/down for disarming. Remove arming switch as it complicates arming gestures logic. Remove MAV_CTRL_SCALE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
2025-08-27 Support arm/disarm mavlink commands Refactor commands handling to remove repeating ack message packing.
2025-08-27 Implement AUTO mode for automatic flights Support SET_ATTITUDE_TARGET, SET_ACTUATOR_CONTROL_TARGET in mavlink. ACTUATOR_OUTPUT_STATUS is changed ACTUATOR_CONTROL_TARGET to match used message for sett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
2025-09-02 Fix rc calibration steps enumeration
    [rc.ino]
2025-09-11 Fix rc calibration steps enumeration again
    [rc.ino]
2025-09-20 Fix fields order in psq command
    [cli.ino]
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2025-09-25 Some fixes and updates in pyflix Fix set_controls Add set_armed method
    [flix.py]
2025-10-03 pyflix: partially fix wireless downloading logs
    [flix.py]
2025-10-03 pyflix: don't quit on any sendto error
    [proxy.py]
2025-10-07 Ensure showing correct raw data in imu command Some IMUs will reset acc and gyro buffer on whoAmI() call
    [imu.ino]
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2025-10-07 Reset yaw target when drone disarmed Prevent unexpected behavior when the drone tries to restore its old yaw on takeoff.
    [control.ino]
2025-10-07 Disarm the drone on simulator plugin reset In order to reset yaw target.
    [simulator.cpp]
2025-10-14 Update VSCode settings Disable error squiggles as they often work incorrectly. Decrease number of include libraries to index.
    [check_c_cpp_properties.py]
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2025-10-19 Rename failsafe.ino to safety.ino To aggregate all the safety related functionality.
    [safety.ino, simulator.cpp]
2025-10-19 Lowercase imu and rc variables To make it more obvious these are variables, not classes.
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2025-10-19 Revert t variable type to float instead of double For the sake of simplicity and consistency.
    [cli.ino, flix.ino, log.ino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]
2025-10-20 Refactor PID control to simplify the code and modifications Each PID uses its internal dt, so may be various contexts with different rate. PID has max dt, so no need to reset explicitly.
    [control.ino]
2025-10-20 Skip attitude/rate control if thrustTarget is ineffective To prevent i term windup.
    [control.ino]
2025-11-06 Add Rate class for running the code at fixed rate
    [log.ino, mavlink.ino, parameters.ino]
2025-11-06 Many updates to documentation Updates to main readme. Add much more info to usage article. Move simulator building to simulation's readme. Improve assembly article. Many fixes. Updates in diagrams.
2025-11-14 Refactor Wi-Fi log download Use MAVLink LOG_REQUEST_DATA and LOG_DATA for download log instead of console. Make Wi-Fi download default way of downloading the log. Make `log` command only print the he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
2025-11-22 Minor updates to pyflix library, pyflix@0.10 Fixes to documentation. Improve logger format.
    [flix.py]
2025-11-22 Move yaw dead zone handling from mavlink to control subsystem So yaw dead zone works the same for rc and mavlink.
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2026-01-13 Documentation and book updates Improve the main list of features. Use lowercase imu variable for consistency with the firmware code. Minor fixes.
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2026-01-22 Support integer parameters in addition to floats The variable pointer is stored as a union field. If `.integer` field is true, then integer pointer should be used. Interfaces to parameters (cli and m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
    [mavlink.ino, parameters.ino]
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2026-01-22 Make parameter names case-insensitive + minor fix
    [parameters.ino, rc.ino]
2026-01-22 Make failsafe configurable using parameters SF_RC_LOSS_TIME - time without rc to activate failsafe. SD_DESCEND_TIME - total time to decrease the throttle to zero. Make controlTime nan on the start to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
    [parameters.ino, rc.ino, safety.ino]
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2026-01-24 Add parameter for configuring gyro bias lpf + reset the filter on `reset` command
    [cli.ino, imu.ino, parameters.ino]
2026-01-24 Fix mavlink parameter set acknowledgement value If the parameter is integer the acknowledgement should contain the rounded value.
    [mavlink.ino]
2026-01-24 Simplify lpf filter code Begin with zero instead of the initializing value, as the latter doesn't make much sense in practice, but complicates the code much.
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2026-01-27 Fix error when launching the sim Also make the parameters WIFI_LOC_PORT and WIFI_REM_PORT work in the sim.
    [wifi.h]
2026-01-27 Add parameters for list of modes bound to rc switch Parameters: CTL_FLT_MODE_0, CTL_FLT_MODE_1, CTL_FLT_MODE_2. Also fix a bug with incorrect choosing the mode from controlMode.
    [control.ino, parameters.ino]
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2026-02-19 Make motor parameters apply without reboot Add callback to parameter definition to call after parameter is changed.
    [motors.ino, parameters.ino]
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2026-04-18 Fix working with parameters in pyflix examples PITCH_P parameter was renamed to CTL_P_P
    [example.py]
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2026-04-23 Fix imu command output Gyro field contained filtered gyro instead of scaled only gyro.
    [imu.ino]
2026-04-23 Minor fix in sys command String works with printf %s, but actually it's a UB.
    [cli.ino]
2026-04-23 Move disabling brown-out code to power subsystem
    [flix.ino, power.ino]
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2026-05-05 Reduce angle drift by adding level correction to the estimator Leverage a priori knowledge that the drone's average attitude is level. Explanation: https://t.me/opensourcequadcopter/158.
    [estimate.ino, parameters.ino]
2026-05-07 Fix imu rotation definition The X axis should be pointing to the mounting holes, not pins side.
    [imu.ino]
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2026-05-07 Fix motors pwm frequency for esp32s3 etc in the docs
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2026-05-10 Fix and improve wifi subsystem Fix a fault when wifi is disabled (udp can't be used without wifi). Print RSSI and channel in wifi command.
    [wifi.ino]
2026-05-12 Remove reboot requirement when changing RC_RX_PIN
    [parameters.ino]
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2026-05-17 Improve voltage measurement Apply PWM_VOLT_PIN without reboot. Check if the voltage pin can be used with ADC when setting up. Set voltage to NAN, when it's unknown (including pyflix). pyflix@0.15. Do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
    [flix.py, mavlink.ino, parameters.ino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]
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2026-05-27 Fix simulator run Add missing extern variables. Fix warning.
    [mavlink.ino, wifi.h]
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2026-05-30 Increase buffer for print, make sys output more correct usStackHighWaterMark is not stack size, it's the minimum stack size
    [cli.ino]
2026-05-30 Replace ps and psq commands with st command + minor changes Re-arrange commands order. Make command parser consider \r in addition to \n.
    [cli.ino]
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2026-06-08 Don't apply level correction on idle thrust
    [estimate.ino]
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2026-06-09 Bring back espnow tx buffering keeping resends disabled Buffering is needed for sending large prints, otherwise the espnow internal buffer overflows. Make onSent always think there was success send, 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
    [wifi.ino]
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2026-06-30 Minor fixes and updates
    [flix.ino, motors.ino]
